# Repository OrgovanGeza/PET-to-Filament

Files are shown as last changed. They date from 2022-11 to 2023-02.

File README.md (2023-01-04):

# PET to Filament
This repository is to document my journey of creating a machine that transforms PET bottles into 3D printer Filament.  
I'm combining existing projects into one, using the best ideas from all worlds:
- Base of the whole project: [Petamentor2](https://petamentor2.com/ "Petamentor2 project's website") by [Ondřej Šraitr](https://www.facebook.com/groups/594548605536945)
- [Bearing Cutter](https://www.youtube.com/watch?v=Mc2vt349XlI&ab_channel=MatthieuSAMSON) by [Mak3D](https://www.youtube.com/@-Mak3D) 
- [Petalot](https://github.com/function3d/petalot "Petalot project's Github page") by [Function3D](https://linktr.ee/function.3d) 

My version is a bit different from the base Petamentor2 project as I used a bearing-style cutter. I also added 2 cooling fans, and switches to every electrical component.

**The pulltruder is built from the following parts:**
- PET bottle cutter
- PET strip guider and cleaner
- Heated nozzle that turns PET strip into filament
- Heatblock & heater to heat the nozzle
- Fans that make the pulltruded strip cooled
- Thermocontoroller that controls the heater
- Motor, and a spool that pulls the PET through the cutter & nozzle, and collects the filament on the spool
- Filament hook tube that connects the puller to the pulled filament
- Motor Speed Controller
- PET strip width controller
- Switches for every component

A lot of parts can be 3D printed, but others has to be purchased.
You can find a summary of every purchasable part and an estimated price for the whole project in the [Hardware summary excel](/Hardware%20summary.xlsx). 

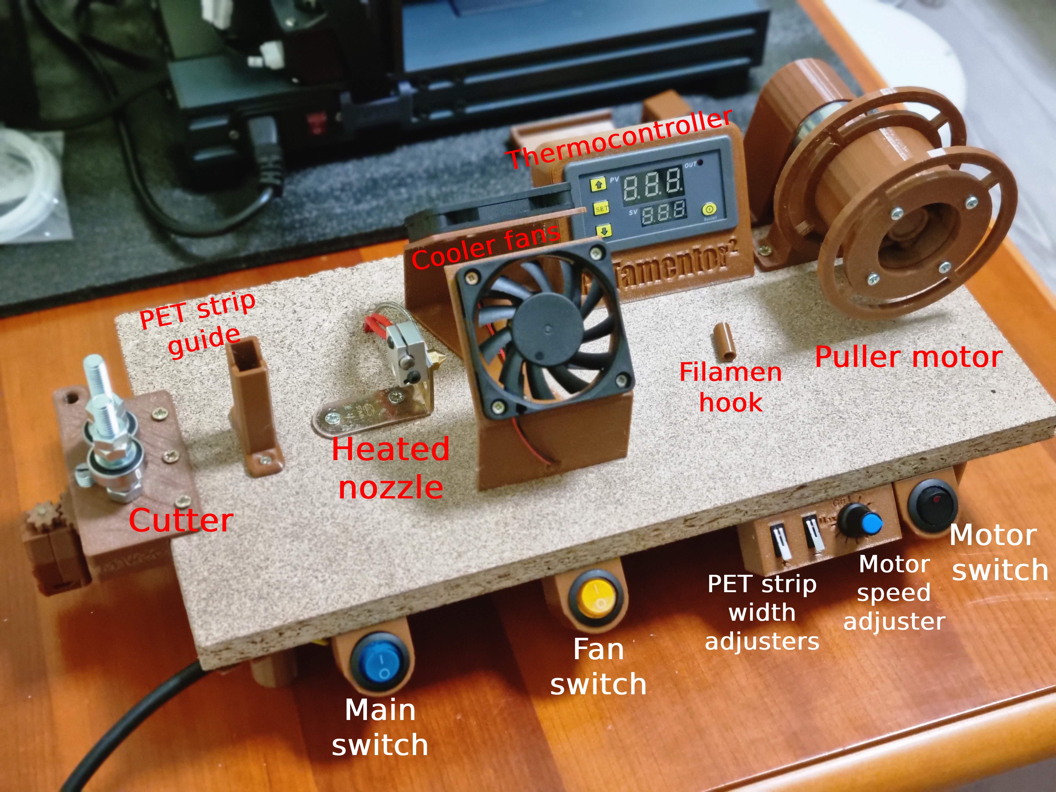
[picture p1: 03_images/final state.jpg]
Parts named
 

The STLs that I have actually used can be found in the [01_STLs folder](/01_STLs/). 

I also included the [gcodes](/02_Gcodes/) for 0.4mm nozzle and PLA, but please always slice your own from the STLs if you can! 

I collected all the STLs, pictures, diagrams from the "base" projects, and put them into their respective folders as well. You will not need them if you will build exactly the version that I built, but I felt like including them in this repo for safe measure.

## The beginnings
I purchased every needed electronic / hardware part, and collected + sliced all the STLs. 
When the packages arrived I re-measured every dimension, and printed the plastic parts.

Some tools that are 100% necessary for the assembly process (other than the ones listed in the hardware list):
- drill with 1.5mm - 8mm drill heads,
- screwdriver with bitheads,
- soldering iron,
- electrical wires,
- heat shrink tubes,
- utility knife.

## Platform with switch holders and adapter
I started the assembly with adding the 4 legs to the corners, and the holders for the controllers and the switches.
After that, I mounted the adapter, and wired it with the main switch.
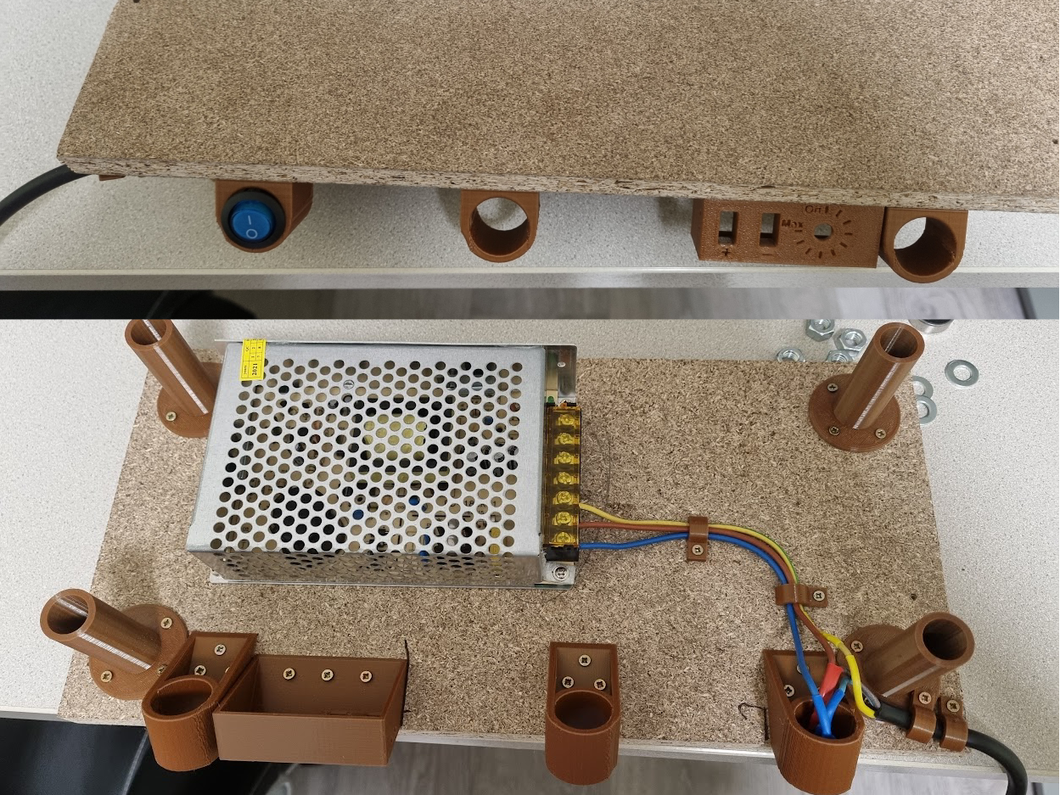
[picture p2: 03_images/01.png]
First steps assembled
 
[Youtube tutorial video of this step. ](https://www.youtube.com/watch?v=9QzTbSUWdYM&ab_channel=Ond%C5%99ej%C5%A0raitr) 
I would consider this as the first "main" checkpoint. From now on, all there is to do is to add the individual electrical parts, and wire them either directly to the adapter, or through a switch / controller. 

## Mounting the electronics and other hardware parts
I started by laying out the parts on the baseplate, and marking where I would want everything to be. After that I pre-drilled the places where the screws would go, plus some bigger holes for the wires that will go through the board.
After that I placed every electronic part in it's 3D printed holder, so that during the wiring process I would know exactly how long the wires have to be.
 
### Cutter and puller motor
I used a bearing-style cutter, but I added the same type of motorized cut-width adjuster. 
It is also a better design as it is not required to drill holes through the board for the width-adjuster screws. All there is to do is to screw the whole 3D printed cutter to the end of the board. 
[Youtube tutorial video of the bearing sharpening process](https://www.youtube.com/watch?v=eTBnhKWMYQk&ab_channel=Function.3d). 
[Youtube tutorial video of the cutter assembly](https://www.youtube.com/watch?v=Mc2vt349XlI&ab_channel=MatthieuSAMSON). 

The assembly process is summarized on [this video](https://youtu.be/2e_wMAU6v-k?t=132) (of course the cutter part is not relevant for this version). 
I ordered some smaller cut-width controller switches, so I had to re-design the holder panel. I designed it in a way that it can be secured to place with the help of some 3D printer filament. I also added some nice indicators of the pull speed.
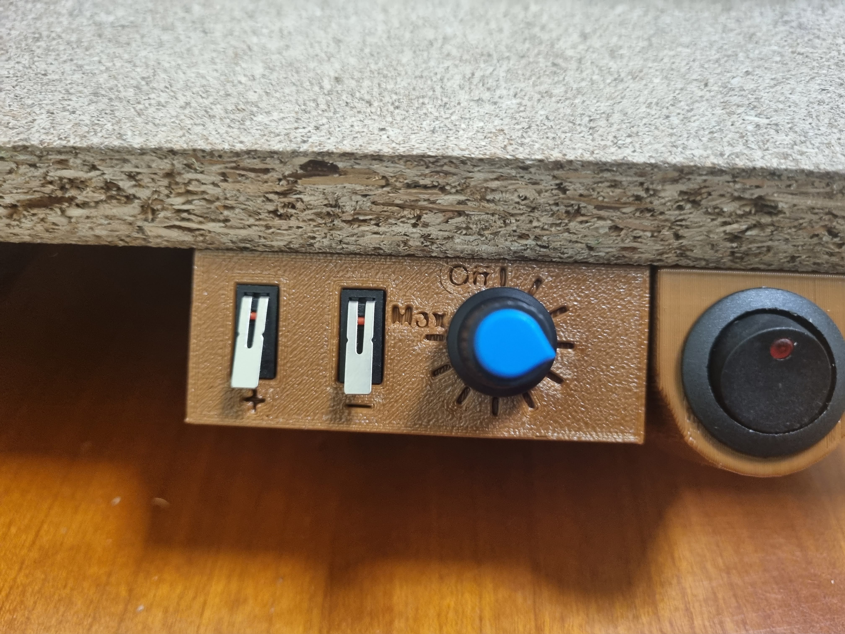
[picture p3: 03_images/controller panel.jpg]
Controller panel
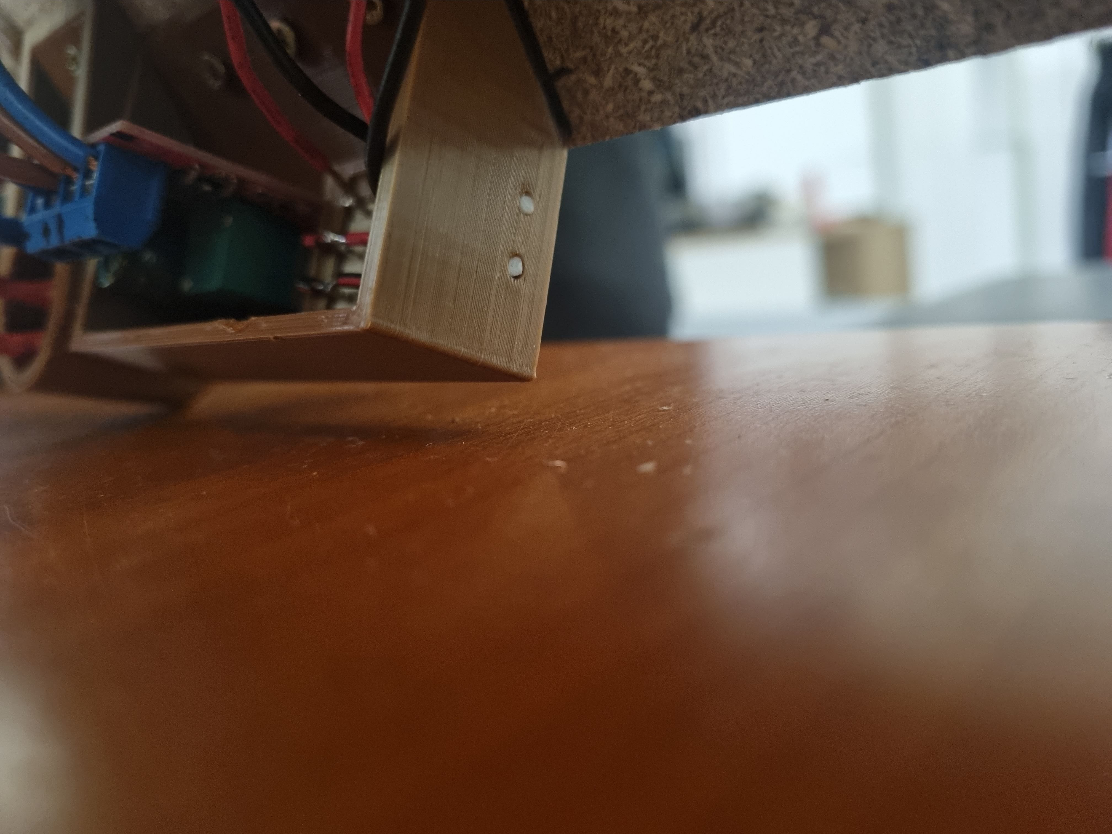
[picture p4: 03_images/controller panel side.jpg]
Controller panel side
  

### Thermocontroller and heatblock 
For the pulltruder to work, we have to modify the heatblock and the nozzle.
If you could purchase a nozzle with a 1.5mm hole, you don't have to modify it, however if you only have a 0.4mm hole on it, you have to drill it with a 1.5mm drill.
I suggest to assemble the heatblock and the nozzle on the L-shape iron, and mount it on a wood sheet (or even on the main board).
Make sure to drill using as slow a speed as possible using a drill bit for metal!

**Steps:**
1. Use a 1.5mm drill to drill the nozzle (if you have a 0.4mm nozzle). Make sure to drill from the heatblock's direction. 
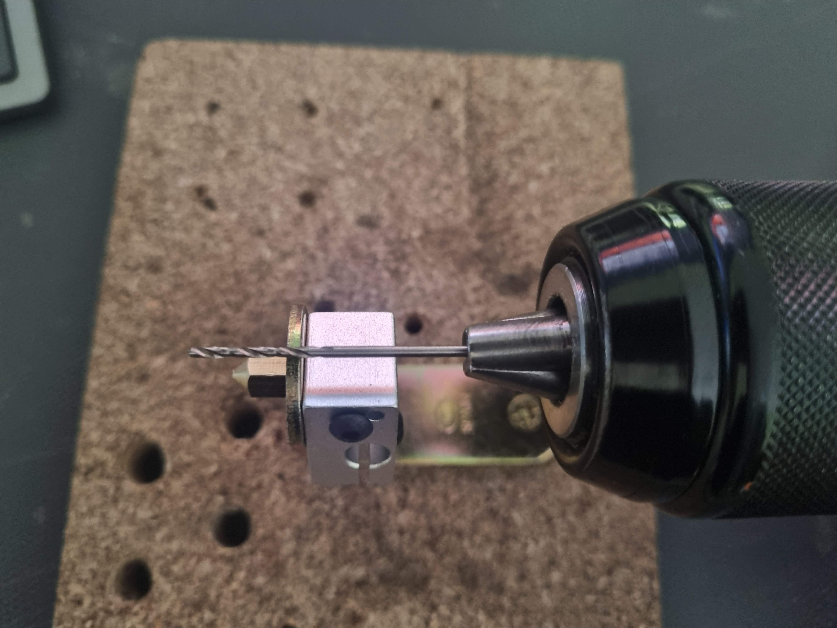
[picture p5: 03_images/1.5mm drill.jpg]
1.5mm drill
 
2. Use a 3mm drill to drill into the nozzle, but only until the cone part begins. 
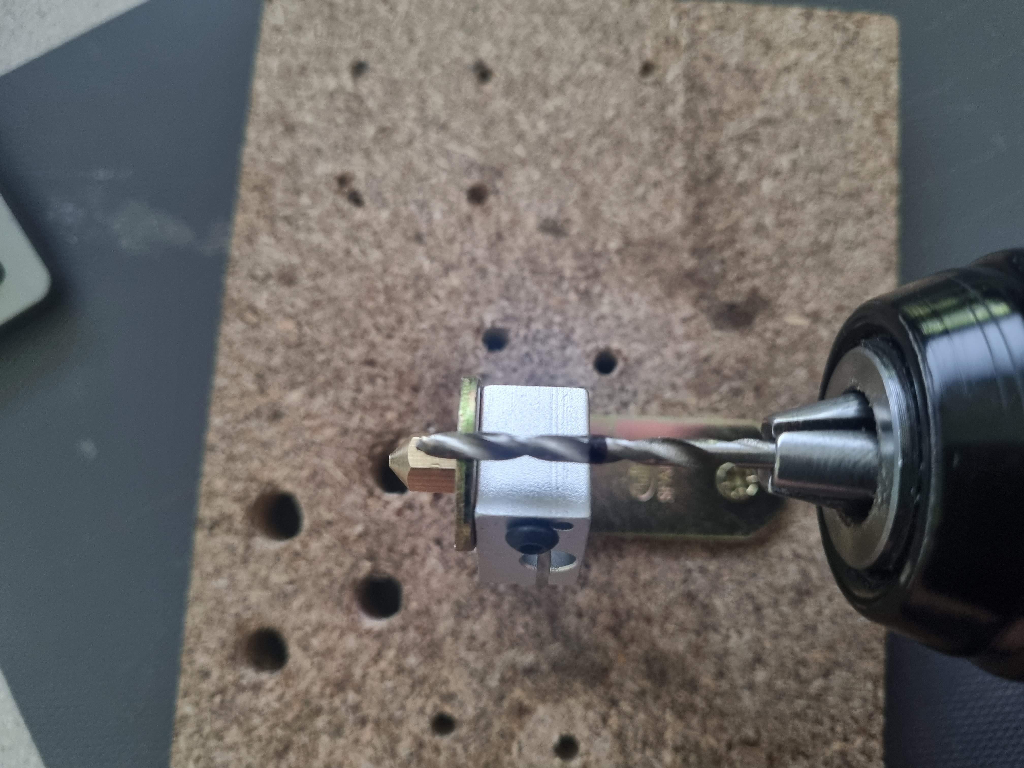
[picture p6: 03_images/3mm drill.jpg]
3mm drill
 
3. Use a 5mm drill to drill the beginning of the nozzle. 
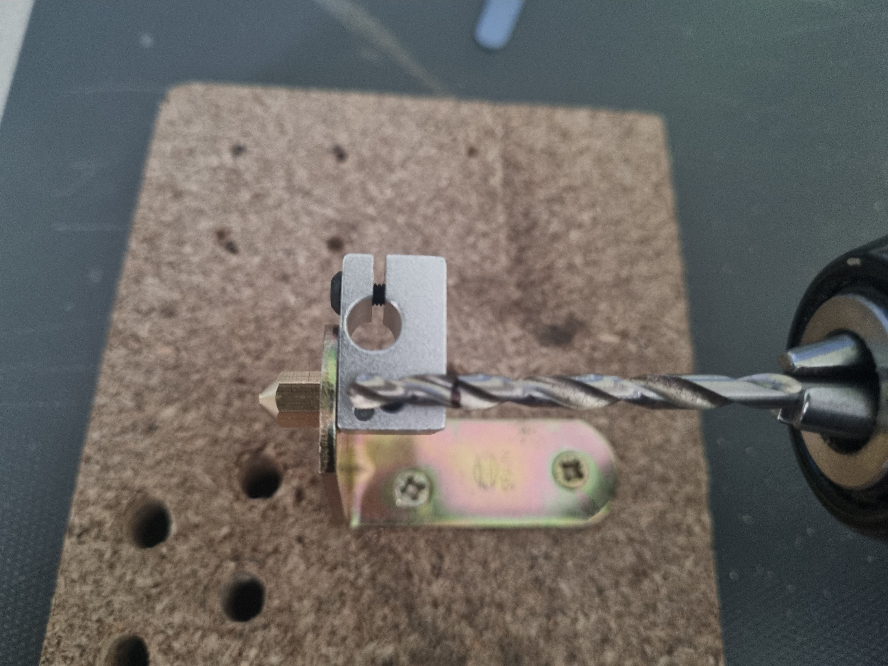
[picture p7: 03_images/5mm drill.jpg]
5mm drill
 
4. Use a 6mm drill to remove the threads from the heatblock. 
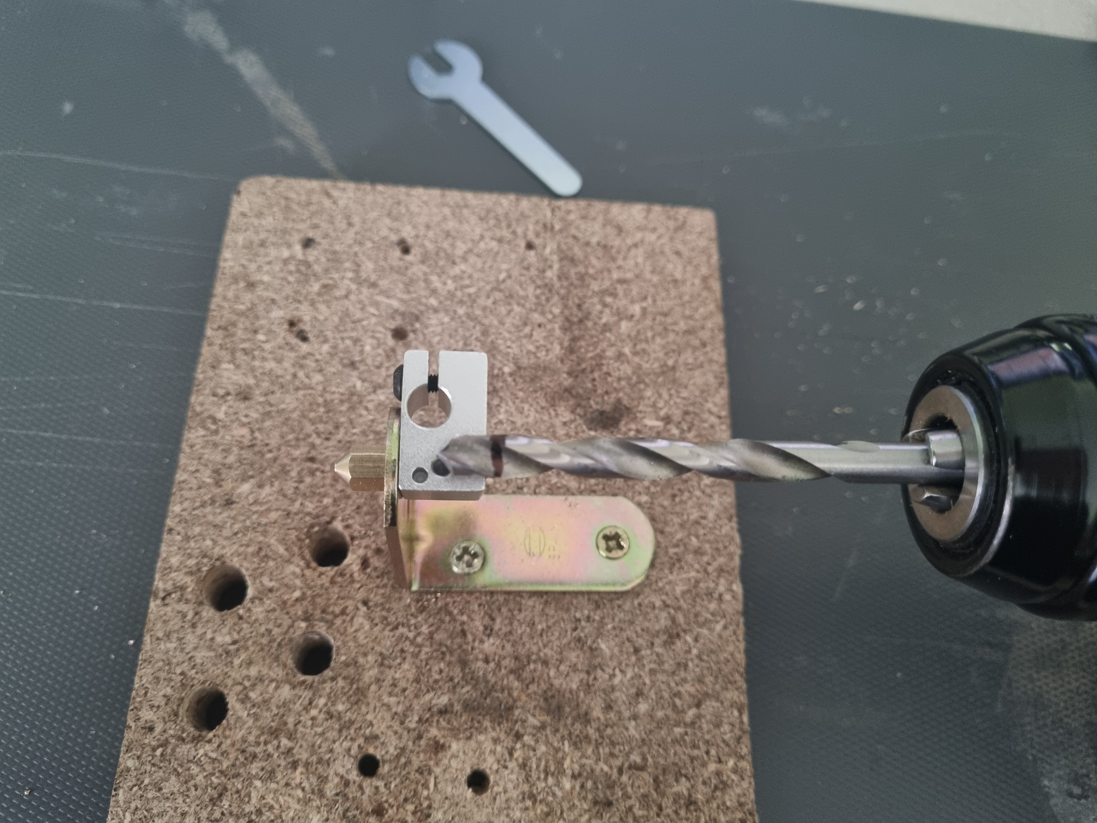
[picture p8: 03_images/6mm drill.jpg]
6mm drill
 
5. Use only the cone part of a 8mm drill to make the beginning of the heatblock wider. 
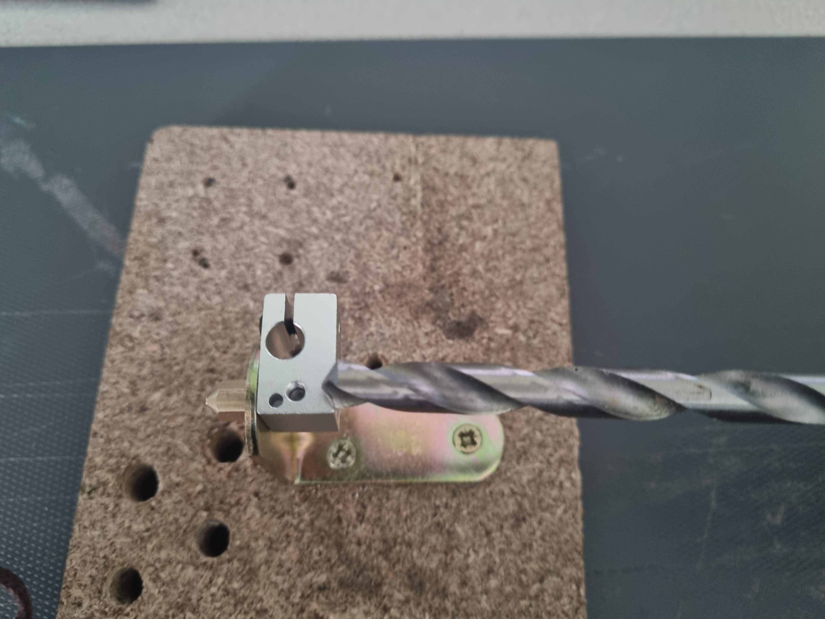
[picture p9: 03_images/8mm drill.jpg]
8mm drill
 

It should look something like this at the end: 
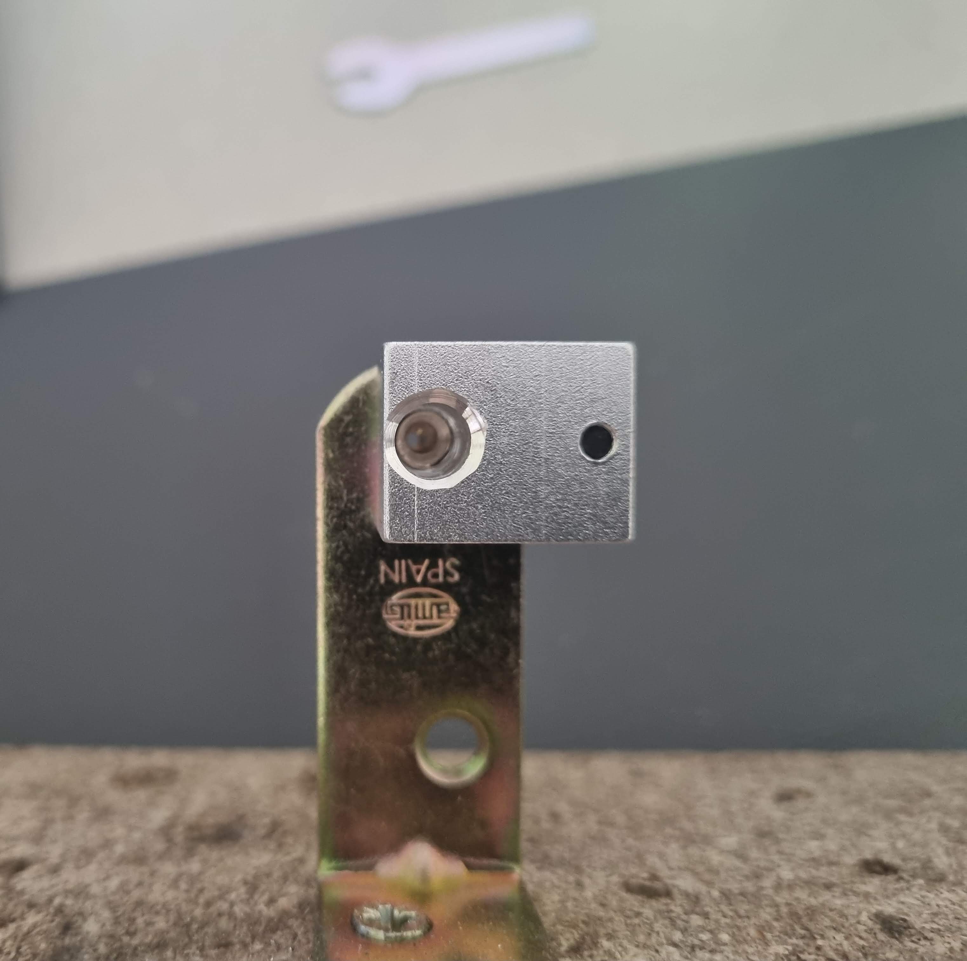
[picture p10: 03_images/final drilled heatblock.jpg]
Final drilled heatblock
 
[Youtube tutorial video of this step](https://www.youtube.com/watch?v=WH65QqU2NoA&ab_channel=Ond%C5%99ej%C5%A0raitr) 

After all this, it is time to screw it onto the board along with the thermocontroller. 
[Youtube tutorial video of this step](https://www.youtube.com/watch?v=RYWRElXa6Fs&ab_channel=Ond%C5%99ej%C5%A0raitr) 

### Fans 
This part is not video-documented, but it's pretty straight-forward. 
I designed a fan-holder frame, printed 2 of it, and screwed onto the board. The fans can be screwed onto it using a 12mm woodscrew. 
I added some holes on the bottom of the frame so that the fan cables can go through it. 
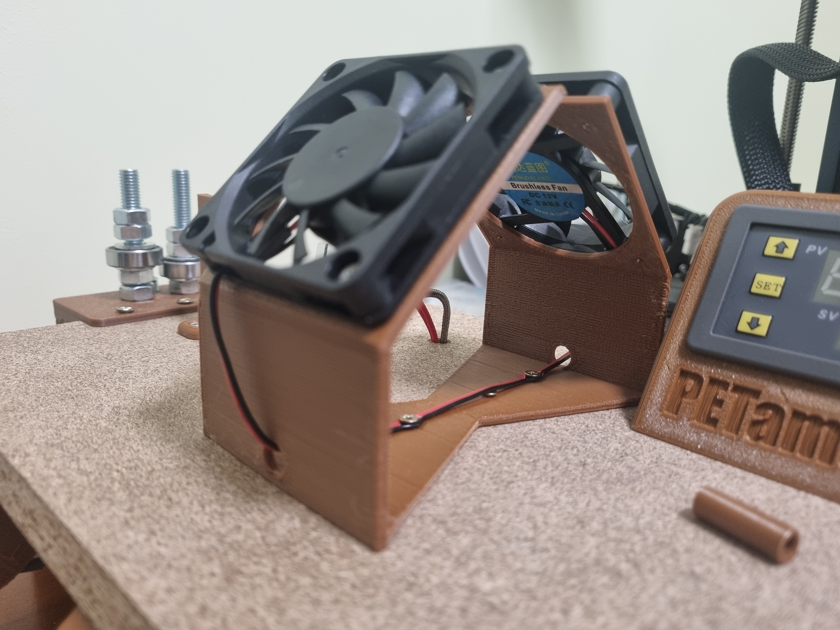
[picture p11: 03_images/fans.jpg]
Fans
 

## Wiring
Of course the wiring had to be done on the bottom of the board, so I fetched some books that I put under the ends of the board so that I could flip it upside down for the soldering-party to start. 
I suggest to use as many cable management hooks as possible to keep everything nice and tidy.

Here is a summary diagram of the whole wiring process: 
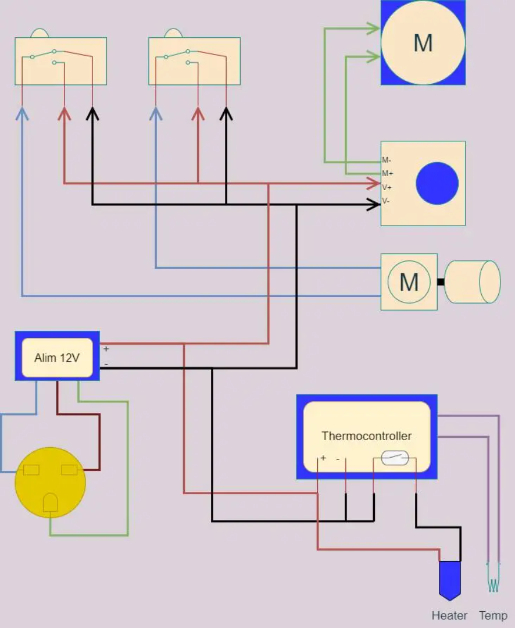
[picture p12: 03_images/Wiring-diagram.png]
Wiring
 
(to be updated with fans and extra switches)

### Switches
The switches are pretty simple to wire. For each electronic component that it will turn on/off you will need to connect one of the wires to the switch, and the other cable can go straight to the adapter. 
The switch has a 3rd leg for the LED that is in the switch itself. You can leave it out from the wiring process, or you can connect the other type of cable than the one that you connected to the other 2 legs. 

Here is a simple explanation image: 
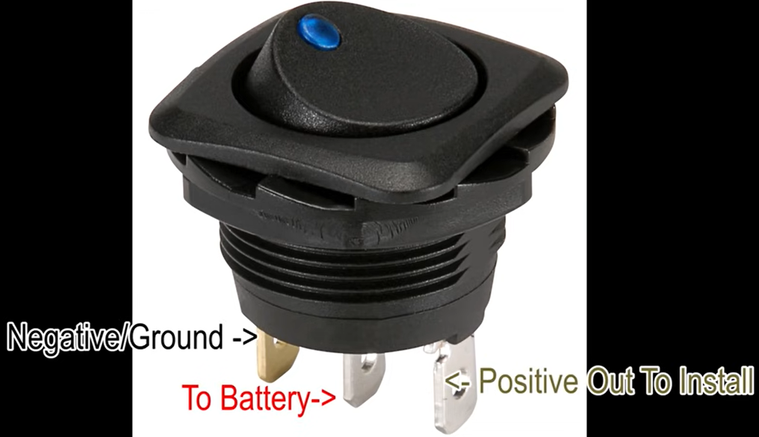
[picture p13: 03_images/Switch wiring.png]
Switch wiring
 

### Controller panel
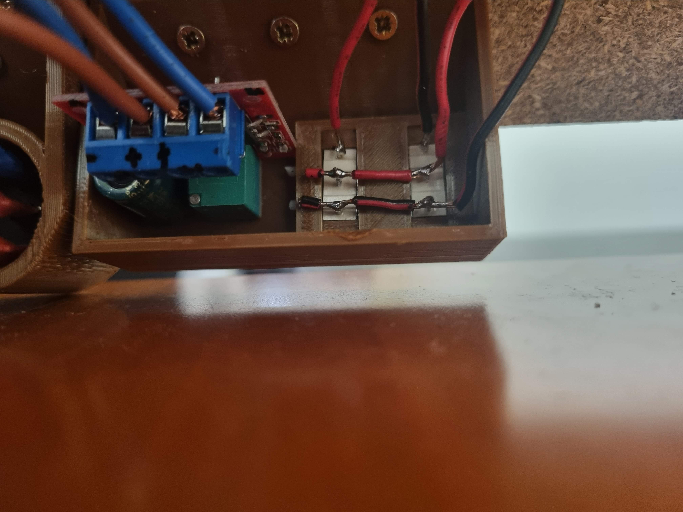
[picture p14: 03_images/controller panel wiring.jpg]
Controller panel
 

This is how it looks like after everything got wired: 
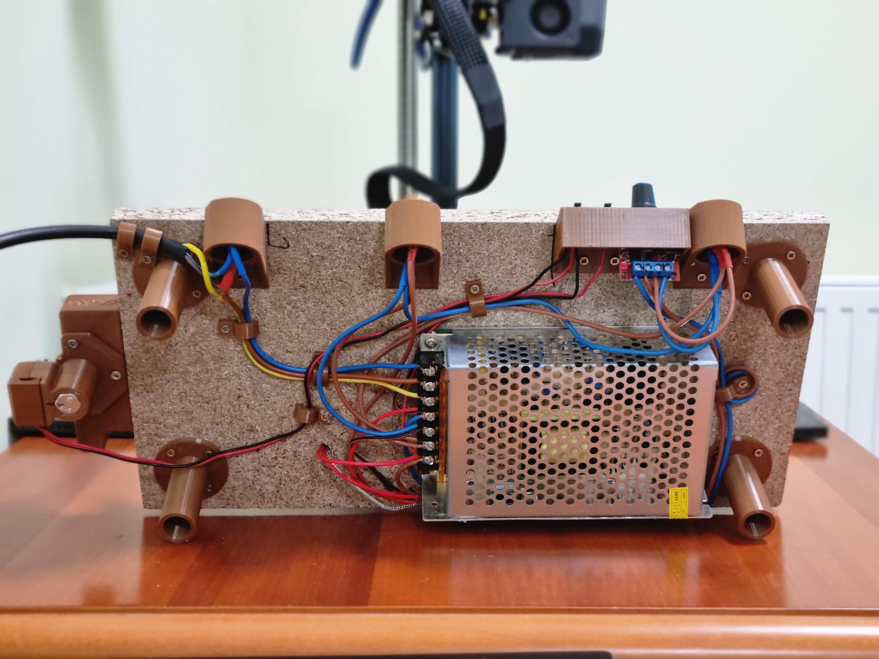
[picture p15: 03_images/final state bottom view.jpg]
wired bottom


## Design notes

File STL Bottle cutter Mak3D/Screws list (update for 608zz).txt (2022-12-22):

Watch the unmount video here :

https://www.youtube.com/watch?v=Mc2vt349XlI

Here the screws list with the chronology of appearance for the 6200zz version :

0.28 - 2x M8 nuts
0.35 - 2x M8 washer
0.41 - 2x 6200zz bearing with 2 printed spacers 
0.46 - 1x M8 washer + 1x M8 nut
0.53 - 2x M8 nuts
1.01 - 2x M8 washer
1.10 - 3x wood screw diameter 4mm length 15mm
1.21 - 2x wood screw diameter 4mm length 15mm
1.33 - 4x M3x10 screw
2.05 - 1x Original PETamentor cutter motor
2.13 - 1x M8x50 screw with a 8mm notch
2.31 - 1x M8 nut
2.40 - 3x M3x10 screw
3.03 - 1x M8x40 + 1x M8x50 screws
3.14 - 3x M3 nuts

You will have to use the 6200zz version of the base... obviously ;)

######################

For the 608zz version,

Identical to the 6200zz version except :

- Use the 608zz base... obviously ;)
- At chronology 1.01, add an M8 washer on the screw of the lowest bearing.
- No need to print the spacers

######################

by Mak3D

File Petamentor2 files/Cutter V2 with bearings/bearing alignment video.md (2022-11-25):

Video that helps with the alignment of the bearings:  
https://www.youtube.com/watch?v=eTBnhKWMYQk&ab_channel=Function.3d

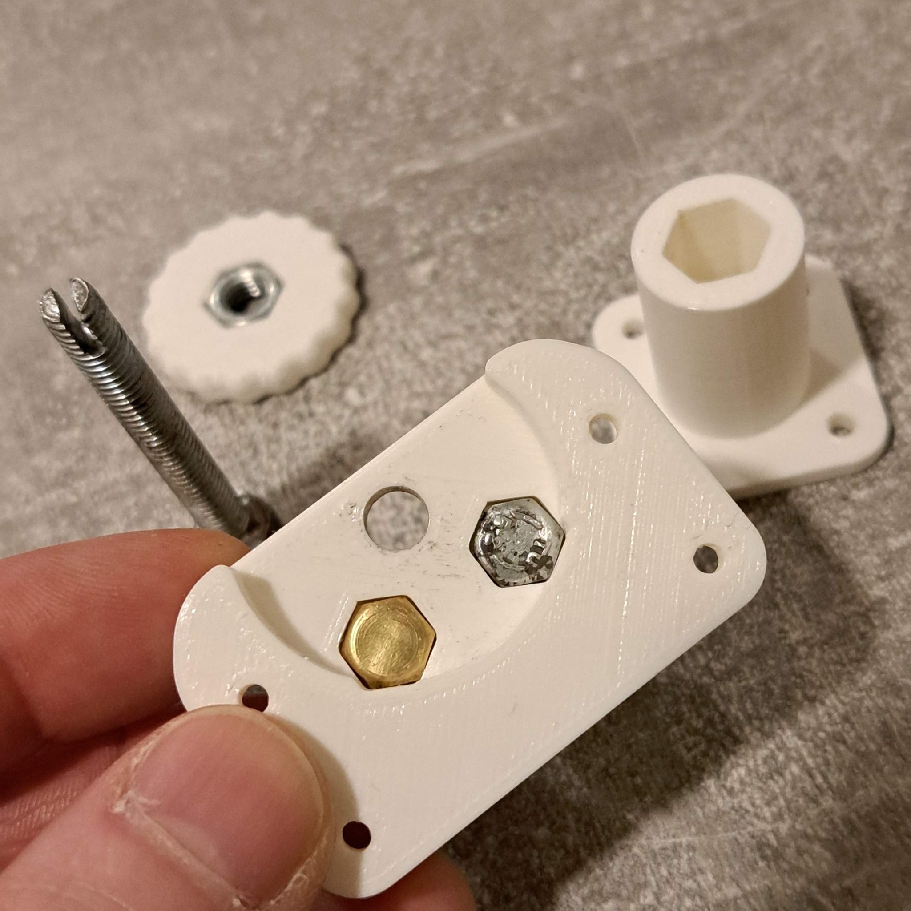
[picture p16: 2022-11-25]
Petamentor2 files/Cutter V2 with bearings/317067126_191194893464056_4027501066497704301_n.jpg

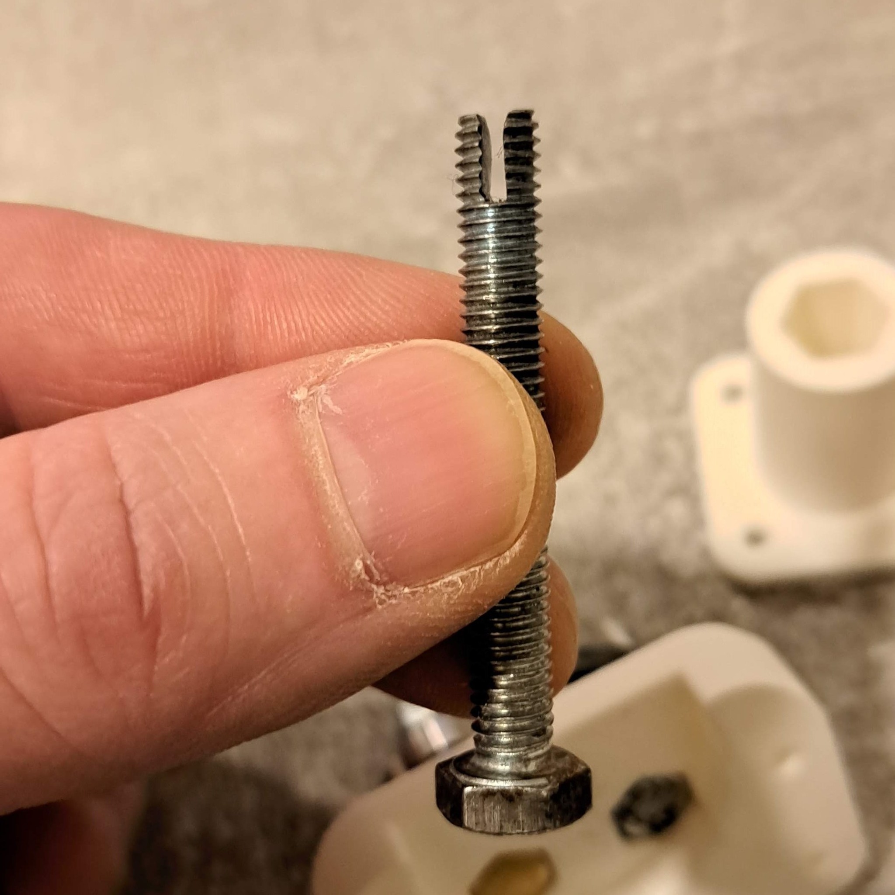
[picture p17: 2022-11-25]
Petamentor2 files/Cutter V2 with bearings/317075406_191194870130725_5858508003684558365_n.jpg

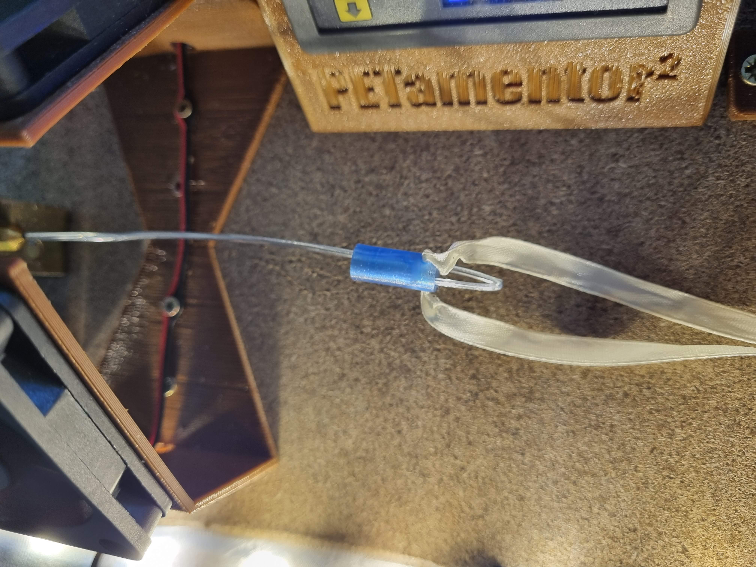
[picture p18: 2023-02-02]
03_images/FilamentHook03.jpg

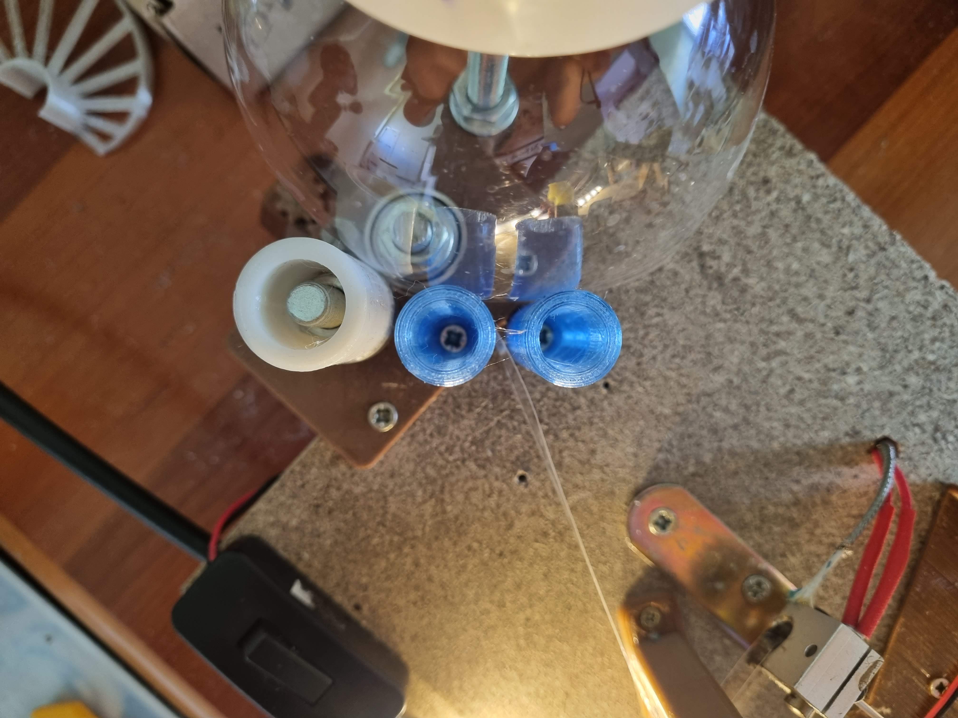
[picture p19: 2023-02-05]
03_images/Bottle_giude_2.jpg

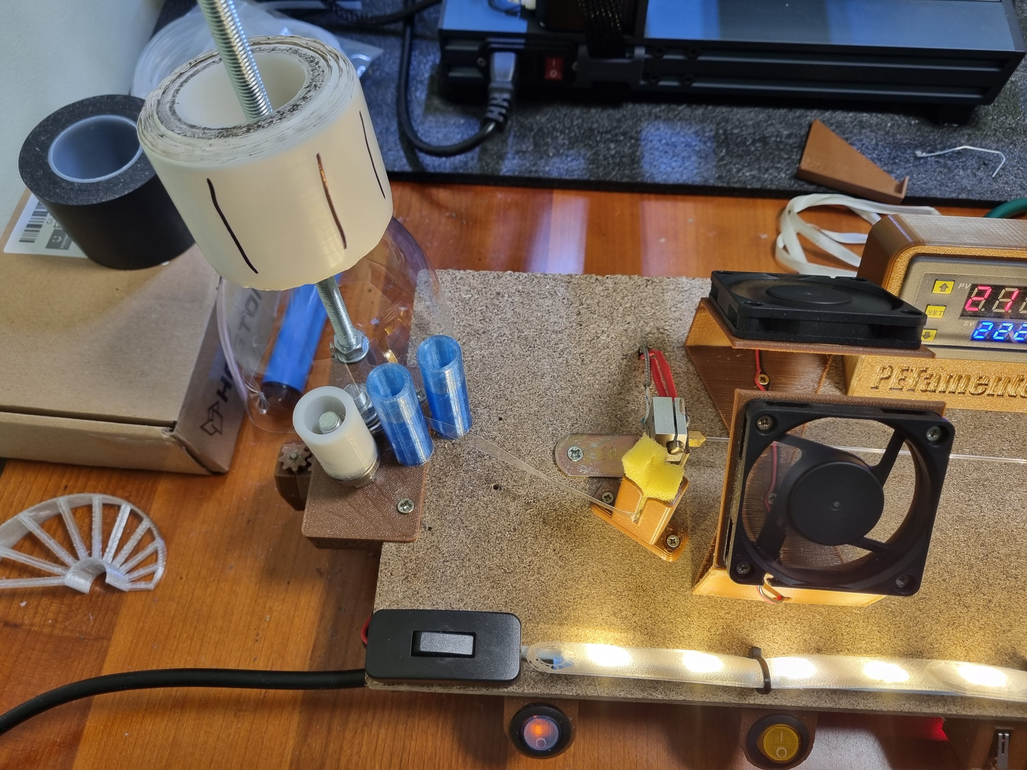
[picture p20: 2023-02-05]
03_images/Bottle_giude_1.jpg

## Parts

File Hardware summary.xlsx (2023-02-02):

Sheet: Summary
This Excel is written in a format that it will give you an estimated cost on top of links to every part.
I advise you to open the Aliexpress links, and then check your local stores to see if you can buy the parts cheaper.
If I linked something outside from Aliexpress, it is my local store where I could purchase the part cheaper. If you can't buy it locally, replace the price with the aliexpress price.
Every price is currently in HUF. You can define your own currency format, puls you can define the exchange rate, and the whole excel file will get updated based on that.
Please modify the green backgrounded fields with the appropriate data relevant for you:
Name of your currency: | USD
Exchange rate: | 1 | USD | IS | 380 | HUF
 | HUF | USD
Sum purchased parts | 23034 | 60.61578947
Sum printed parts | 3674.8656 | 9.67
SUM | 26708.8656 | 70.28648842

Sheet: Parts to buy
Category | Name | Description | link |  | pcs | price sum [HUF] | price sum [USD]
ELECTRONICS | Power supply 12V 10A (120W) | You can use 5A and also 10A. The difference is in the stability of the engine speed and the stability of the nozzle temperature. The stronger the source, the faster the nozzle heats up. | aliexpress (https://www.aliexpress.com/item/33051556213.html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) | BivinMarket (https://www.bivin.hu/ipari-tapegyseg-12v-10a-7409) | 1 | 3790 | 9.97
 | 12V (7RPM) DC motor | The motor is built into the holder and drives the spool for winding the finished pet filament. This 12V DC motor has its own gearbox (it is not necessary to print the gearbox). This means very high torque without any additional gear system. | aliexpress (https://www.aliexpress.com/item/1005003273734490.html?spm=a2g0o.cart.0.0.394838da4cVxUh&mp=1) |  | 1 | 3661 | 9.63
 | PWM Regulator 12V 5A | PWM 12V DC Motor Speed Controller Module DC-DC 4.5V-35V Adjustable Speed Regulator. This small component allows for a smooth reduction or increase in engine speed without loss of torque. | aliexpress (https://www.aliexpress.com/item/1005003742615772.html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) |  | 1 | 1100 | 2.89
 | Thermocontroller (12V – up to 500°C) | Simple wiring, simple remoting temperature. No hacks, no struggle. Be careful on params. You need 12V one with working temperature up to 500C! | aliexpress (https://www.aliexpress.com/item/1005003256576173.html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) |  | 1 | 3950 | 10.39
 | 12V N20 (300RPM) | Geared 12V (300RPM) DC motor for cutter. This part is moving cutter blade up and down with worm gear 3D printed gear system. The 300 RPM is good speed/torque foe easy, and slow moving the blade up and down. | aliexpress (https://www.aliexpress.com/item/4000274747864.html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) |  | 1 | 1524 | 4.01
 | Heater 12V (40W) | Ceramic heater 12V (40W) is a component that is inserted into the heat block and ensures heating of the nozzle. It is a cheap and simple component. | aliexpress (https://www.aliexpress.com/item/32817471679.html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) |  | 1 | 950 | 2.50
 | Microswitch (2PCS) | Two pieces of microswitches for controlling the height of the cutter blade. The height of the knife blade determines the width of the cut strip from the PET bottle. This will give you the ideal width due to the differences in wall thickness of different bottles. | aliexpress (https://www.aliexpress.com/item/10000002013575.html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) | hestore (https://www.hestore.hu/prod_10029907.html) | 2 | 200 | 0.53
 | Color Switch (230V) | The colored power switch used in the previous version of PETamentor. It is important that the switch is sized for the power of your socket. If your local network is 110V, you can safely use a switch for 230V, never the other way around! | aliexpress (https://www.aliexpress.com/item/32850626943.html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) | hestore (https://www.hestore.hu/prod_10038585.html) | 3 | 702 | 1.85
 | 12V fan | It is important to cool down the filamen as soon as it gets through the noozle in order to avoid further deformation 60x60x10mm | aliexpress (https://www.aliexpress.com/item/4001122850071.html?curPageLogUid=Flv8Qw5RIGqx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) | hestore (https://www.hestore.hu/prod_10041708.html) | 2 | 1932 | 5.08
3D printer parts | Heatblock | The heat block is the part heated by the heating element (12V 40W). When choosing, it is important to know that the larger the block, the slower it cools with less temperature fluctuations. | aliexpress (https://www.aliexpress.com/item/10000352512040.html?scm_id=1007.13339.291025.0&scm-url=1007.13339.291025.0) |  | 1 | 957 | 2.52
 | 3D printer Nozzle (1.5mm) | To convert a PET bottle into filament, I use a standard nozzle with a diameter of 0.4 mm, which must be drilled. Drilling is very simple, using a 1.5mm drill bit. You can buy a 1.5mm nozzle on aliexpress, and you don't have to drill. | aliexpress (https://www.aliexpress.com/item/32836645391.html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) |  | 1 | 480 | 1.26
Hardware | Base wood plate size cca: 45-50cm x 20 cm x 1-2cm | 48 * 18 * 2 | bakosfa | Check your local hardware store | 1 | 520 | 1.37
 | Metal Bracket | L shape metal bracket (20×20) for mouting a heatblock with the nozzle. Hole is little bit tight, so its better to drill it with 6mm drill bit (only for a nozzle). | aliexpress (https://www.aliexpress.com/item/32934551326.html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) | Check your local hardware store | 1 | 100 | 0.26
 | M3 Screws (10mm) | Screws for cutter assembly, puller assembly and spool assembly. The screw is 10mm long – metric M3 type. D-fejű metrikus csavar 3*10mm | bakosfa 9 HUF/pcs | Check your local hardware store | 23 | 207 | 0.54
 | M8 bolts (~60mm) | Bolts for the cutting mechanism to modify the cutter height, and for holding the bearings Hatlapú metrikus csavar M8 * 60mm | bakosfa 85 HUF/pcs | Check your local hardware store | 3 | 255 | 0.67
 | M8 nuts | Nuts for securing the bearings and adjusting the cutter height | bakosfa 16 HUF/pcs | Check your local hardware store | 5 | 80 | 0.21
 | M6 Threaded Rod (500mm) optional: 2pcs washer + 2pcs nut | M6 threaded rod – length 500mm, needed for cutter. I personally shortened the rod to 450mm. But that depends on your local conditions. | bakosfa | Check your local hardware store | 1 | 520 | 1.37
 | Bearings (OD 20-22mm, ID 8-12mm) | For the cutting bottle we need 2 bearing that we modify in a way that they have an edge. 608RS or similar | aliexpress (https://www.aliexpress.com/item/1005004970362275.html?curPageLogUid=DeuLNwKBcxg1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) | onlinecsapagy (https://www.onlinecsapagy.hu/termekeink/termekeink/61900_2rs_kn) | 2 | 1470 | 3.87
 | Wood screws M2.6 (10-12mm long) max 4mm diameter | Wood screws that are for attaching all the 3D printed parts of the PETamentor. The wood screws must not be longer than the thickness of your wooden platform. 2.5*12mm 6HUF/pcs 2.5*16mm 6HUF/pcs 3.5*16mm 9HUF/pcs | bakosfa | Check your local hardware store | 48 | 288 | 0.76
 | Silicone tube | For the done filament to be welded together. 1mm inner * 3mm outer diameter. You have to drill it with 1.5mm drill ~1m is needed to weld together 1kg worth of filament, if you use 2cm/weld | Bondex (https://szilikonwebaruhaz.hu/id/00068---248-1-x-3-mm-szilikon-cso) | Check your local hardware store | 3 | 348 | 0.92
 |  |  |  |  | SUM purchased parts (https://petamentor2.com/parts/) | 23034 | 60.62
 |  |  |  |  | click the text above to see the original list on Petamentor2 website

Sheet: Printed parts
I own a 3D printer, these prices might be a bit higher if you hire someone to print these for you.
If you measure how much electricity your printer uses in 60mins, and add how much electricity costs in your country, this Excel will calculate the corect estimate.
My local conditions |  |  |  | Your local conditions
1kWh | 72 | HUF |  | 1kWh |  | USD | If you add all 3 of these, the summary page will use your numbers instead of mine
Printer electricity usage in 60mins | 0.126 | kWh |  | Printer electricity usage in 60mins |  | kWh
1000g filament | 8680 | HUF |  | 1000g filament |  | USD
Part | Quantity [pcs] | Time/pcs [min] | Weight/pcs [g] | Price/piece [HUF] | Price/piece [USD] | Sum price [HUF] | Sum price [USD]
Cable organizer | 6 | 7 | 0.75 | 7.5684 | 0 | 45.4104 | 0
Colorswitch holder | 3 | 62 | 13.52 | 126.728 | 0 | 380.184 | 0
Cutter (all parts) | 1 | 250 | 51.47 | 484.5596 | 0 | 484.5596 | 0
Fan holder | 2 | 60 | 14.77 | 137.2756 | 0 | 274.5512 | 0
Filament guide + cleaner | 1 | 64 | 8.51 | 83.5436 | 0 | 83.5436 | 0
Filament hook tube | 1 | 6 | 0.61 | 6.202 | 0 | 6.202 | 0
Leg | 4 | 54 | 13 | 121.0048 | 0 | 484.0192 | 0
Motor (all parts) | 1 | 427 | 92.4 | 866.5944 | 0 | 866.5944 | 0
Motor speedcontroller holder | 1 | 85 | 16.04 | 152.0792 | 0 | 152.0792 | 0
Spool (all parts) | 1 | 264 | 54.69 | 514.626 | 0 | 514.626 | 0
Thermocontroller | 1 | 180 | 41 | 383.096 | 0 | 383.096 | 0
 |  |  |  |  | SUM | 3674.8656 | 0.00

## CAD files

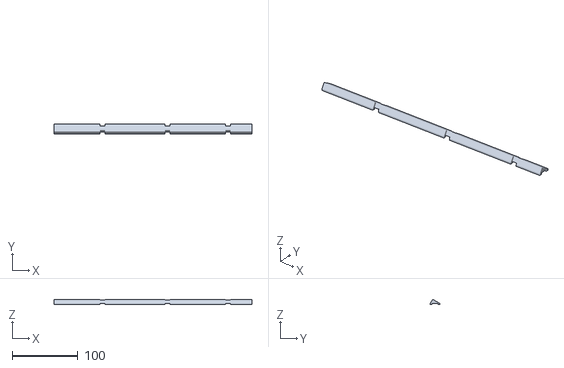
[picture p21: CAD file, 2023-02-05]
01_STLs/LED holder.stl
300.0 x 14.5 x 8.28

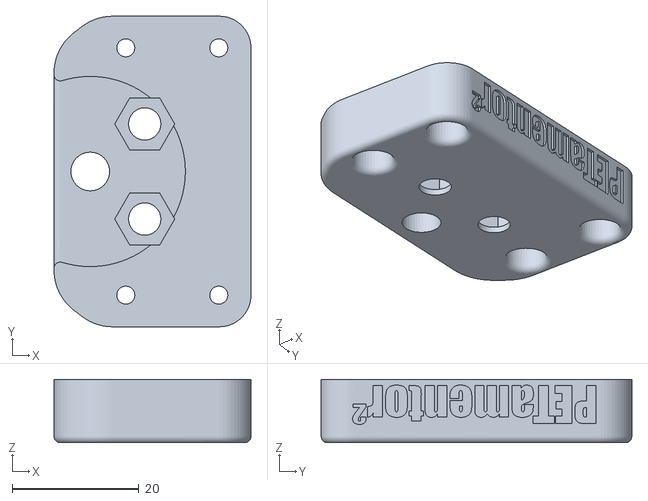
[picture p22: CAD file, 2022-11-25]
Petamentor2 files/Cutter V2 with bearings/Top part.stl
31.1 x 49.0 x 10.0

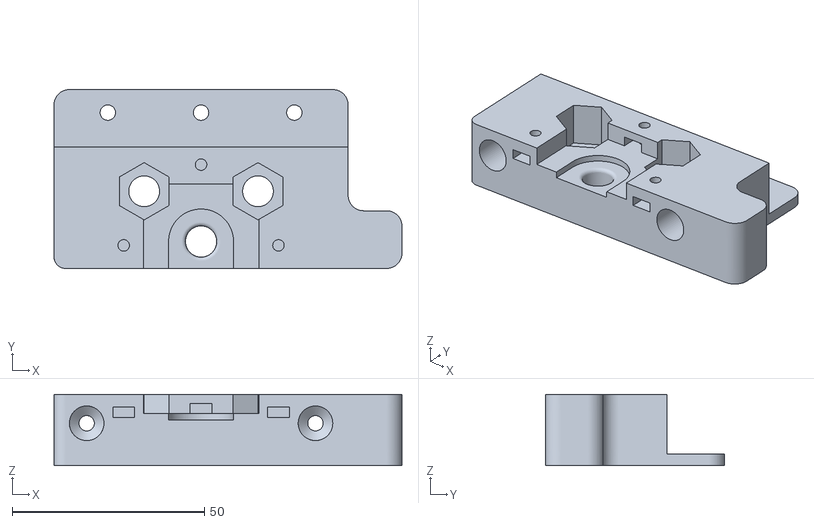
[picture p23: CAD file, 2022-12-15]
STL Bottle cutter Mak3D/Base_6200zz.stl
90.5 x 46.5 x 18.5

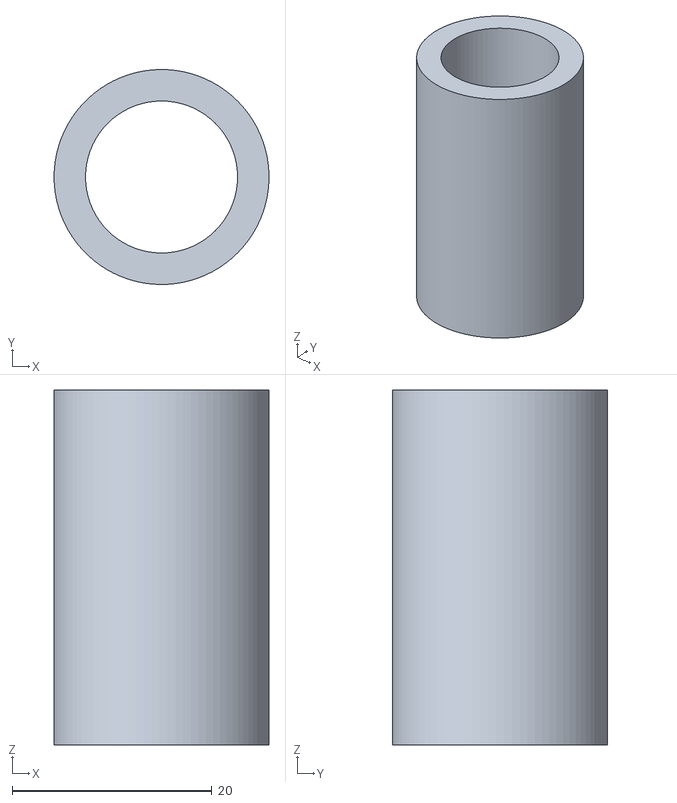
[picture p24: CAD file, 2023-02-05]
01_STLs/Bearing spacer.stl
21.5 x 21.5 x 35.5

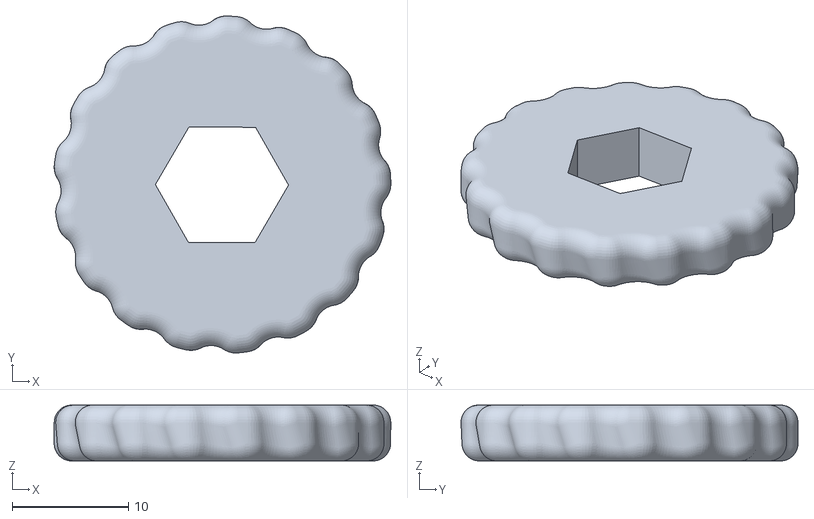
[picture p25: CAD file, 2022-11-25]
Petamentor2 files/Cutter V2 with bearings/Adjust Wheel.stl
28.9 x 28.9 x 4.80

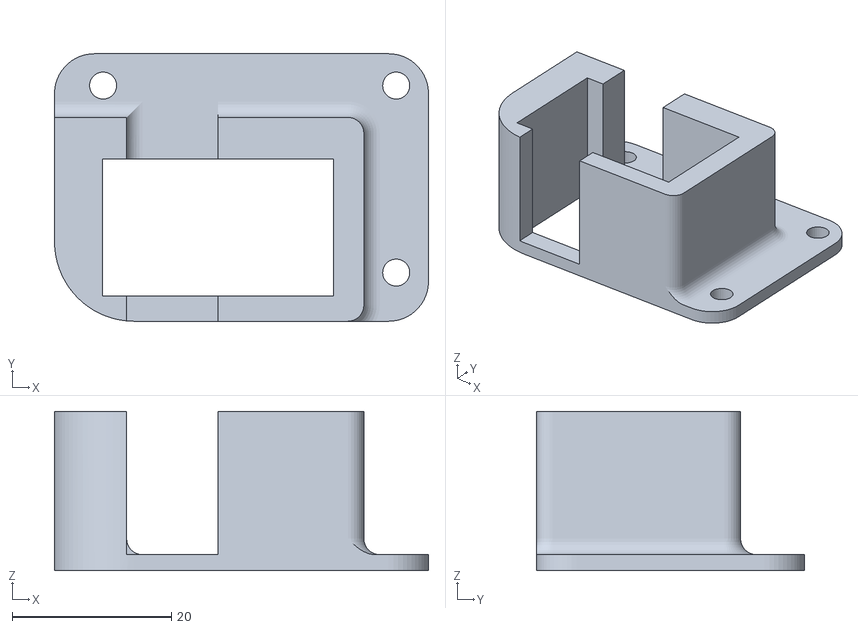
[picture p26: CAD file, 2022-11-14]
Petamentor2 files/STL files/Cutter_-_back_blade_guide.stl
47.0 x 33.6 x 20.0

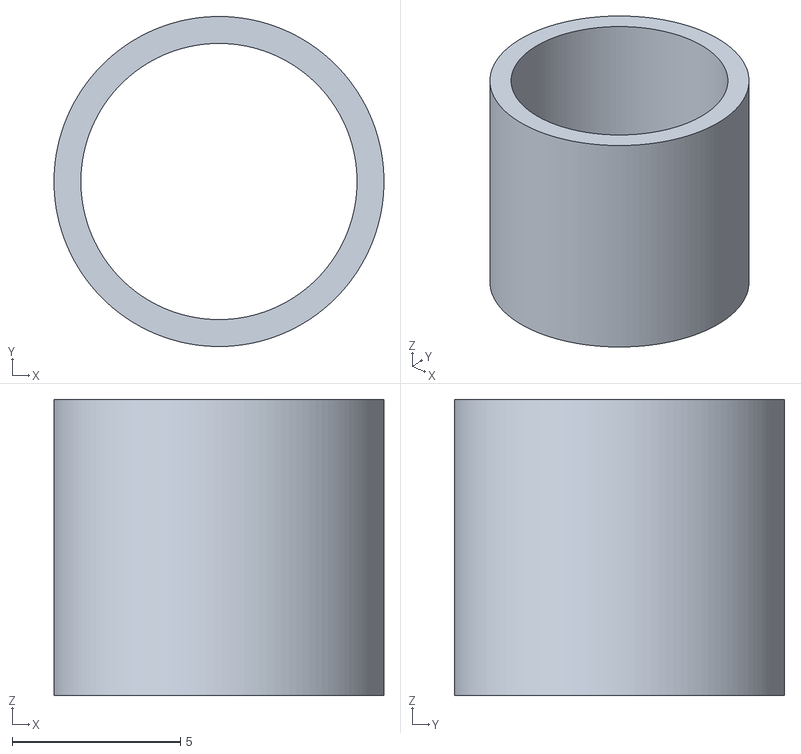
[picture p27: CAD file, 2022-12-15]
STL Bottle cutter Mak3D/Entretoise_6200zz (x2).stl
9.80 x 9.80 x 8.80

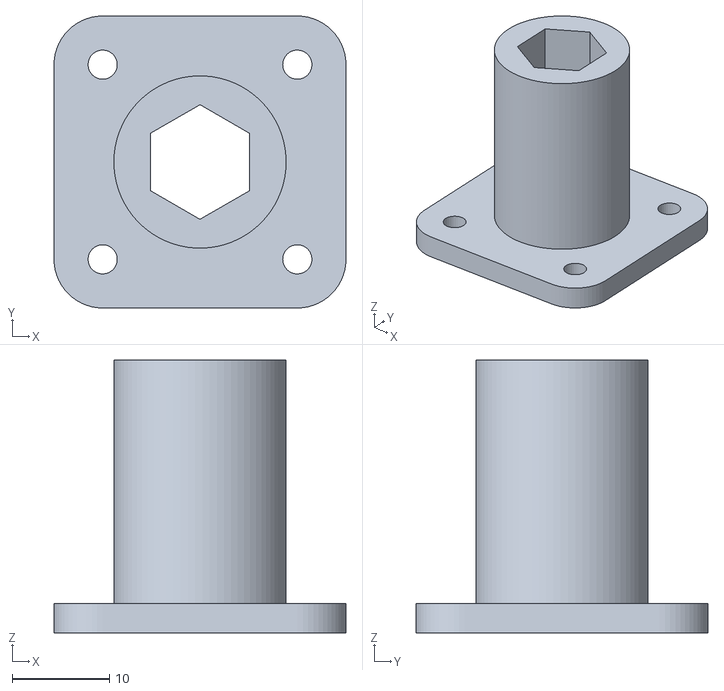
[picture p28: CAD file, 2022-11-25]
Petamentor2 files/Cutter V2 with bearings/Bottom part.stl
30.0 x 30.0 x 28.0

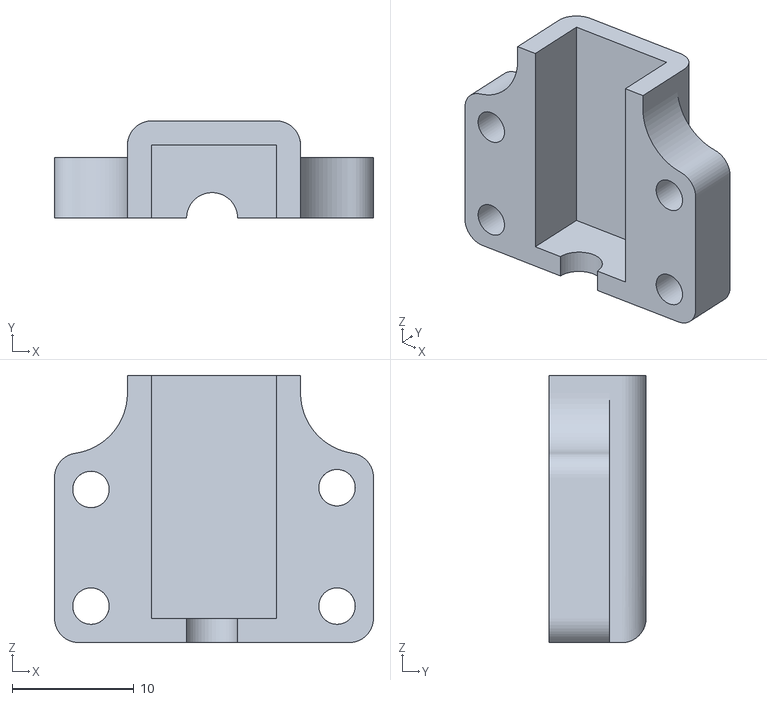
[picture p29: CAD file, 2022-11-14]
Petamentor2 files/STL files/Cutter_-_motor_bracket.stl
26.2 x 8.00 x 22.0

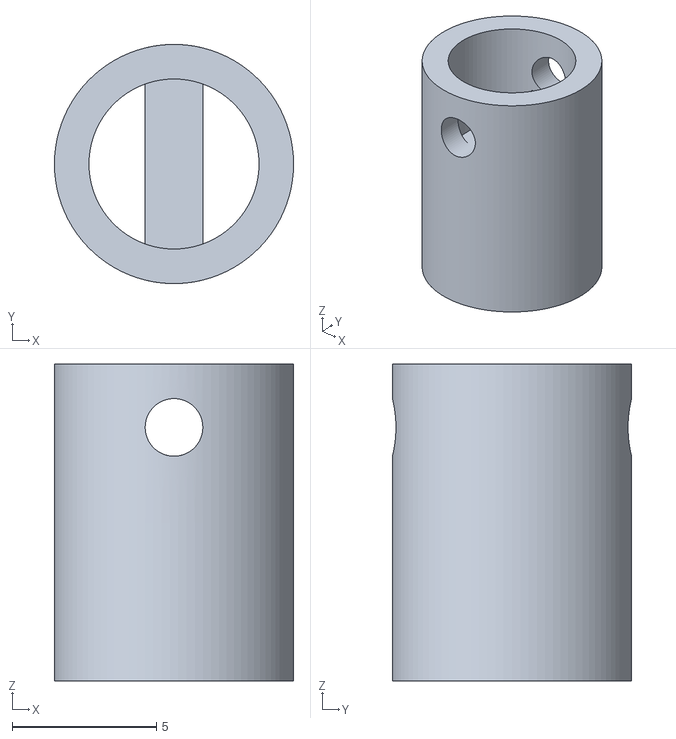
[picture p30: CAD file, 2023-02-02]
01_STLs/Filament hook for 1.75mm Filament V3.stl
8.30 x 8.30 x 11.0

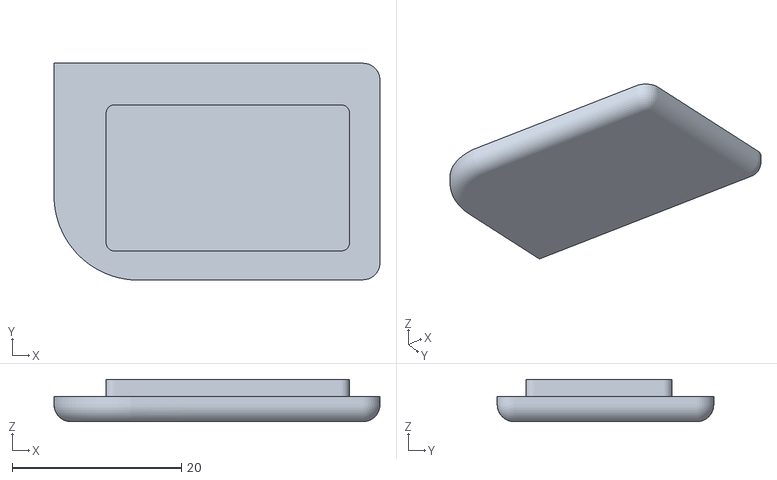
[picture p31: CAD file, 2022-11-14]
Petamentor2 files/STL files/Cutter_-_front_blade_cap.stl
38.6 x 25.6 x 5.00

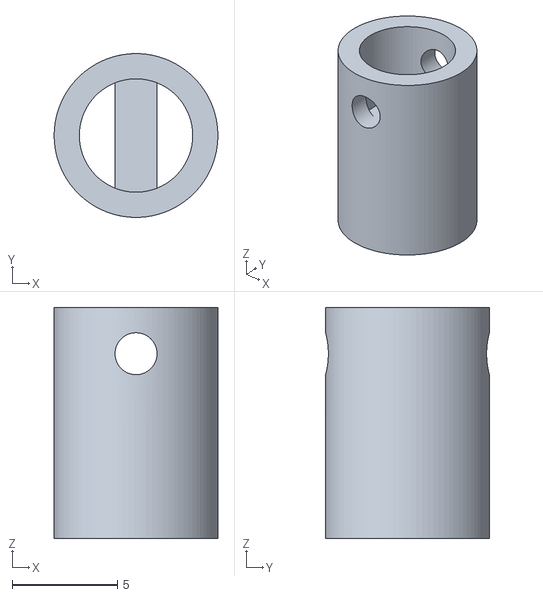
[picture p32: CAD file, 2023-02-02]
01_STLs/Filament hook for 1.5mm Filament V3.stl
7.80 x 7.80 x 11.0

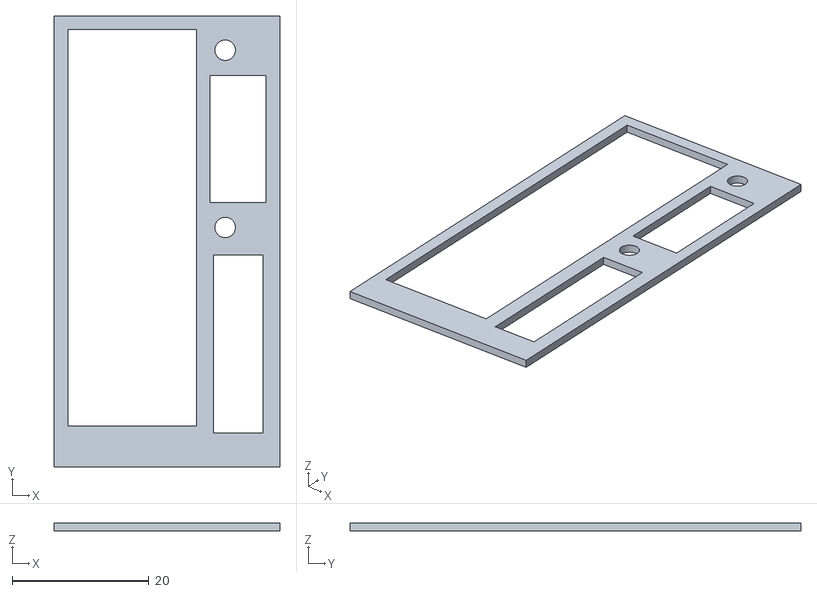
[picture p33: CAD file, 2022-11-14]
Petamentor2 files/STL files/stencil_for_drilling_cutter_holes.stl
33.0 x 65.9 x 1.20

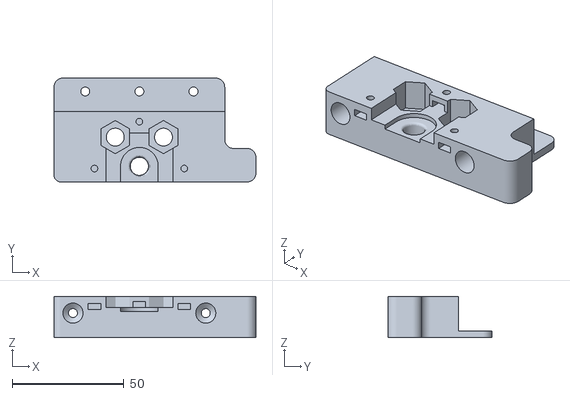
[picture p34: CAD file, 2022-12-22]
01_STLs/Cutter_Base_for_608zz_bearings.stl
90.5 x 46.5 x 18.5

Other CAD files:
Petamentor2 files/STL files/Cutter_-_worm_gear.stl
01_STLs/Fan_holder.stl
Petamentor2 files/STL files/Cutter_-_middle_wheel.stl
01_STLs/Motor_Speedcontroller_holder.stl
01_STLs/Cable_organizer.stl
01_STLs/Colorswitch_holder.stl
01_STLs/Cutter_big_gear.stl
01_STLs/Cutter_bolt_guide.stl
01_STLs/Cutter_motor_cap.stl
01_STLs/Cutter_small_gear.stl
01_STLs/Filament_guide_and_cleaner.stl
01_STLs/Filament_hook_tube.stl
01_STLs/Leg.stl
01_STLs/Motor_Joint.stl
01_STLs/Motor_Mount_back.stl
01_STLs/Motor_Mount_front.stl
01_STLs/Screwable bottle guide.stl
01_STLs/Spool_back.stl
01_STLs/Spool_front.stl
01_STLs/Thermocontroller.stl
Petamentor2 files/STL files/Cutter_-_back_blade_cap.stl
Petamentor2 files/STL files/Cutter_-_base.stl
Petamentor2 files/STL files/Cutter_-_blade_holder.stl
Petamentor2 files/STL files/Cutter_-_front_blade_guide.stl
Petamentor2 files/STL files/Cutter_-_lid.stl
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

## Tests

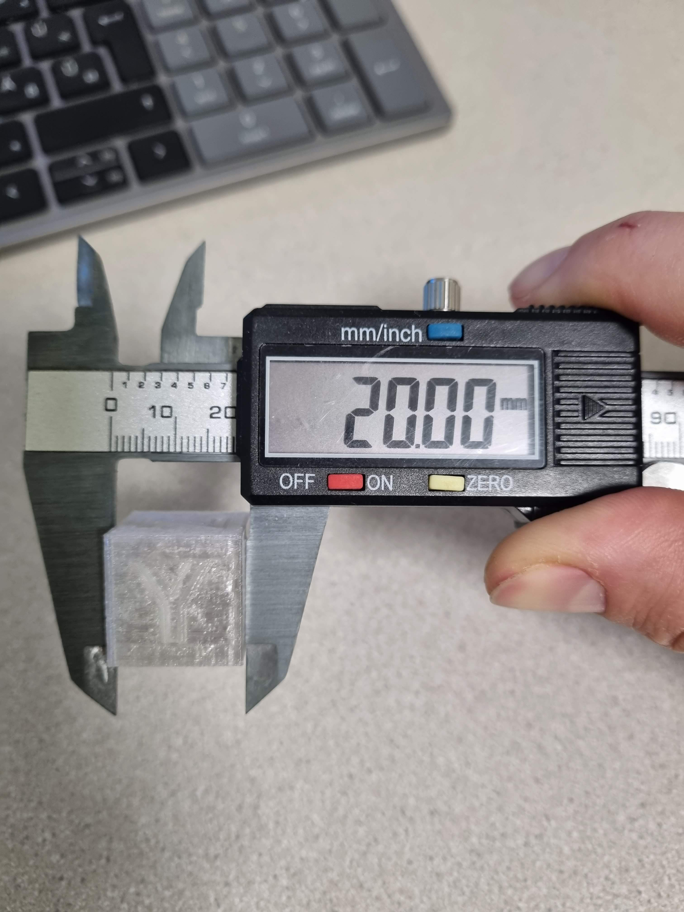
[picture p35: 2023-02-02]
03_images/first calibration cube print.jpg

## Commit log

2022-11-14 Added STL files
    [filament hook tube.stl, pet guide base.stl, pet guide cap.stl]
2022-11-14 added STL
2022-11-14 added hardware summary excel
    [Hardware summary.xlsx]
2022-11-14 added wiring diagram picture
2022-11-23 updated hardware summary
    [Hardware summary.xlsx]
2022-11-25 added cutter with bearings
    [Adjust Wheel.stl, Bottom part.stl, Top part.stl]
2022-11-29 updated parts list
    [Hardware summary.xlsx, filament guide.stl]
2022-11-29 added Fan to hardware list
    [Hardware summary.xlsx]
2022-12-14 started ignoring hardvare summary
    [Hardware summary.xlsx]
2022-12-14 added needed STLs
    [Cutter_-_M8_threaded_rod_holder.stl, Cutter_-_MS_switch_bracket.stl, Cutter_-_button_minus.stl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]
2022-12-14 renamed folders
    [Cutter_-_M8_threaded_rod_holder.stl, Cutter_-_MS_switch_bracket.stl, Cutter_-_button_minus.stl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]
2022-12-15 Updated readme with bearing cutter by Mak3D
2022-12-15 added Bearing Cutter by Mak3D
    [Base.stl, Capot_moteur.stl, Coulisse.stl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]
2022-12-16 updated files
    [Cutter_-_MS_switch_bracket.stl, Cutter_-_button_minus.stl, Cutter_-_button_plus.stl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]
2022-12-18 added FanHolder file
    [Fan_holder.stl]
2022-12-22 added bearing cutter files
    [Base.stl, Base_608zz.stl, Base_6200zz.stl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]
2022-12-31 updated readme with drilling steps
2022-12-31 added picture of drilled heatblock
2023-01-01 added fan picture
2023-01-01 wiring summary
2023-01-01 added wiring diagram
2023-01-03 Added hardware & price summary
    [Hardware summary.xlsx]
2023-01-03 Harmonized naming convention
    [Cable_organizer.stl, Colorswitch_holder.stl, Cutter_Base_for_608zz_bearings.stl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]
2023-01-03 fixed printable quantities
    [Hardware summary.xlsx]
2023-01-03 switch wiring explanation included
2023-01-04 added styling for better readability
    [Hardware summary.xlsx]
2023-02-02 uploaded at 02/02
    [Hardware summary.xlsx]
2023-02-02 over-engineered hook to connect pulltruded filament with the spool
    [Filament hook for 1.5mm Filament V2.stl, Filament hook for 1.75mm Filament V2.stl]
2023-02-02 picture of how to use the filament hook
2023-02-02 update: made the tube half the height for better performance
    [Filament hook for 1.5mm Filament V3.stl, Filament hook for 1.75mm Filament V3.stl]
2023-02-02 removed outdated files
    [Filament hook for 1.5mm Filament V2.stl, Filament hook for 1.75mm Filament V2.stl]
2023-02-05 for keeping the bottle from collapsing
    [Bearing spacer.stl, Screwable bottle guide.stl]
2023-02-05 LED strip holder
    [LED holder.stl]
